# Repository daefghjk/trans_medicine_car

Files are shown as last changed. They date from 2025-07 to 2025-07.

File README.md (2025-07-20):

# 流程
## 基础  
1、小车1上电，摄像头识别初始数字，进入巡线模式，小车1等待药品放入后启动，到达近端病房，等待药品卸载后给摄像头发‘m’，开始返程  
2、同1  
  
## 拓展  
1、小车1上电，摄像头识别初始数字，进入巡线模式，小车1等待药品放入后启动，到达中端病房，检测小车2，等待摄像头发送中端信息‘m‘，小车1判断拓展第几题，发送给小车2；小车2收到后等待药品放入，放入后，且摄像头识别到数字转为巡线模式，开始启动，到1号病房，到了之后点亮黄色LED，发送给小车1，小车1收到信息而且药品卸载后启动返程，发送给小车2熄灭黄色LED，回到药房后发送给小车2，小车2收到后发给摄像头‘m’，走到目标病房。  
  
2、小车1上电，摄像头识别初始数字，进入巡线模式，小车1等待药品放入后启动，到达远端病房，检测小车2，等待摄像头发送远端信息‘f’，小车1判断拓展第几题，发送给小车2；小车2收到后，等待小车1的启动信息，小车1卸载药品后发给摄像头‘m’，开始返程，并发给小车2启动信息，小车2启动，到1号病房等待小车1的启动信息，等到小车1回到药房，发送给小车2启动信息，小车2收到后发给摄像头‘m’，启动到目标病房，亮红色。  
  
拓展1与2的主要差别在：  
1、拓展1小车1需要在小车2到达1号病房后才启动，拓展2小车1不需要等待小车2。  
2、拓展1小车2在小车1未卸载药品就启动，拓展2小车需要等待小车1开始返程才启动。  
  
# K230与小车1与小车2之间的通信协议
K230与小车数据包格式：0xFF、标志位、数据、0xFE  
标志位意义：  
0x00：发送路口方向，此时数据即命令，见下表  
0x01：发送巡线偏移角度，此时数据为字符串形式的浮点数  
0x02：发送到达中端还是远端病房，此时数据即命令，见下表  
  
小车之间数据包格式：0xFF、命令、0xFE  
  
| 方向 | 内容 |
| ---- | ---- |
|车->K230| 0x00 'm' 开启巡线模式|
|K230->车| 0x00 's' 停止电机<br>0x00 'f' 启动电机路口直行<br>0x00 'l' 路口左转<br>0x00 'r' 路口右转<br>0x00 'b' 到达病房<br>0x00 'y' 到达药房<br>0x02 'm' 到达中端病房<br>0x02 'f' 到达远端病|
|小车1->小车2|'1' 目前是拓展1<br>'2' 目前是拓展2<br>'t' 测试是否有小车2<br>'f' 小车2启动<br>'n' 小车2熄灭黄色LED|
|小车2->小车1|'r' 回传确认存在小车2<br>'b' 拓展1确认小车2到达1号病房

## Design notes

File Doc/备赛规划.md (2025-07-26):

## 软件

建个仓库把m0的各种库装进去

直流电机、步进电机、无刷电机、舵机、机械臂

编码器、巡线（灰度）、mpu陀螺仪、

oled、串口屏、

存储器eeprom、

视觉识别（k230、opencv）：颜色形状、误识别、数字（找点例程）、巡线、其他模型的训练和部署

串口、iic、spi、pid、adc、dac、

## 硬件

常见的板子

小车拓展板：4个编码电机、两个舵机、oled、两个串口、陀螺仪、按键和指示灯等，变压

机械臂拓展板：6个舵机/步进电机，

步进电机拓展板：

电源板：引出很多电源线

黑板/红板/嘉立创板之间的转接板

## 机械

问一下能不能借到3d打印机

sw设计

固定k230的支架

机械臂

车架

舵机水平转动的东西

## 其他要买的东西

无线烧录器

考虑一下嘉立创的m0核心板

大车架的常规车轮

## 做题

待选：三子棋、送药小车、激光控制、车位停车

综合测评

用m0做送药小车

研究一下机械臂

## 时间线（暂时）

| 一 | 二 | 三 | 四 | 五 | 六 | 日 |
| ---- | --- | --- | --- | --- | --- | --- |
| | | 2 | 3 | 4 | 5 | 6 |
| | | 今天 | | 研究m0资源和引脚 | 孙艺离开 | 下载程序到m0<br>画拓展板 |
| 7 | 8 | 9 | 10 | 11 | 12 | 13 |
| 视觉 | 视觉 | 视觉<br>把上次的库都拿出来，简单分类 | 孙艺回来 | ，<br>看看freeRTOS， | | |
| | | 16 | | 18 | | 20 |
| | | | 送药小车做完 | 孙艺离开 | | 孙艺回来 |
| | | 23 | | | | |
| | 搞机械臂 | 差不多放元件清单 | | | | |
| | | 30 | 31 | 1 | 2 | 3 |
| | | 开始比赛 | | | 比赛结束 | |

| 模块 | 功能描述 | 具体器件/接口 |
| :---: | :---: | :---: |
| 主控模块 | 系统运算与控制核心 | STM32F103C8T6（ARM Cortex-M3内核） |
| 显示模块 | 时间/日期/闹钟状态可视化 | 8位共阴极LED数码管（动态扫描驱动） |
| 输入模块 | 用户交互入口，支持模式切换、参数校准、闹钟设置 | 4×独立按键（K1-K4）：K1（模式切）、K2（+）、K3（-）、K4（确认） |
| 提醒模块 | 闹钟触发时声音提示 | 无源蜂鸣器（接GPIO输出） |
| 时钟基准 | 提供1Hz计时信号 | 定时器TIM2（配置为1ms中断，累计1000次） |

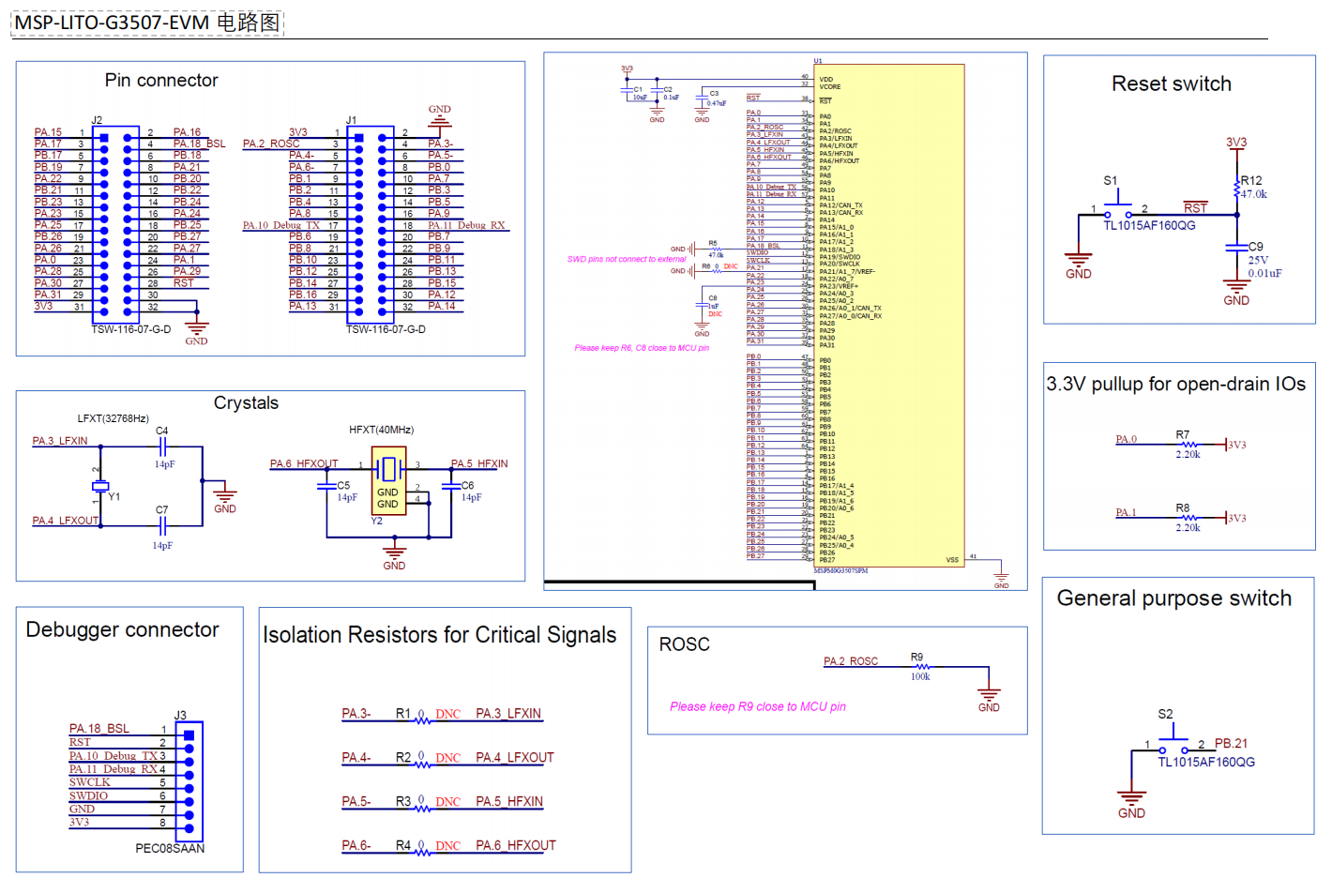
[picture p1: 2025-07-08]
Doc/LITO原理图.png

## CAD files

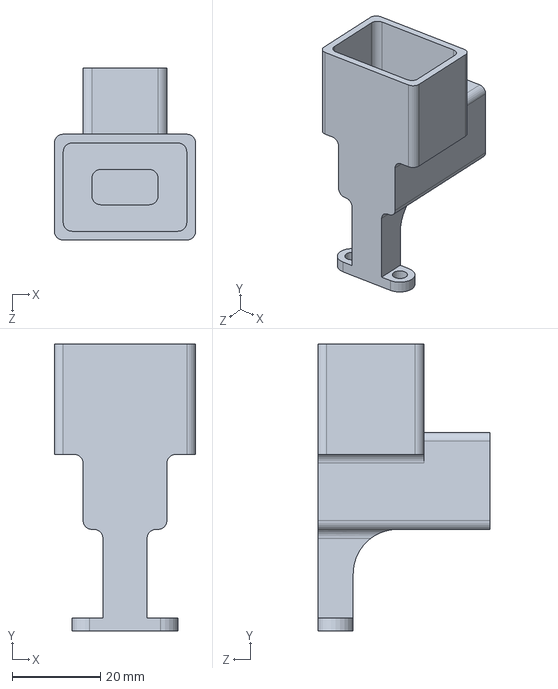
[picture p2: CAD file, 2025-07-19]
2021E硬件/药品放置件.SLDPRT
32.0 x 65.0 x 39.0 mm

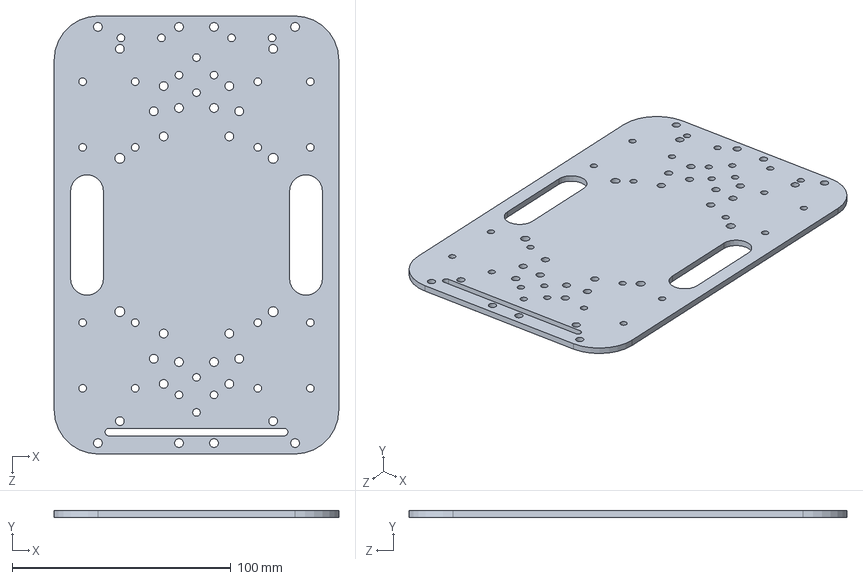
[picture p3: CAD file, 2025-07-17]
2021E硬件/车架.SLDPRT
130.0 x 3.00 x 200.0 mm

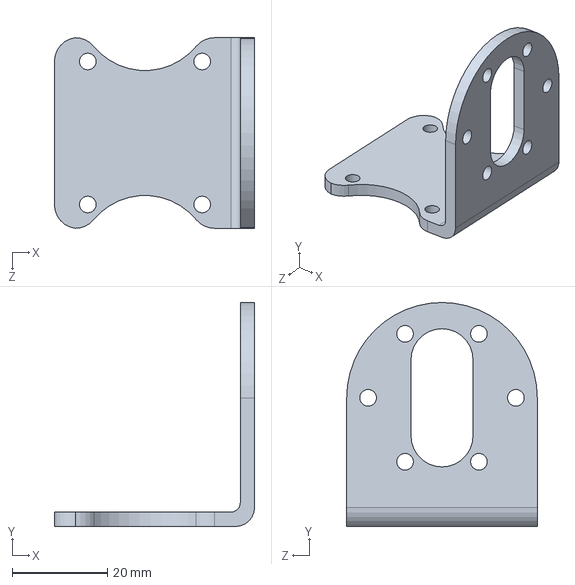
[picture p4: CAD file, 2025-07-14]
2021E硬件/电机固定件.SLDPRT
42.0 x 47.0 x 40.0 mm

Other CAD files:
2021E硬件/电机固定件.3MF
2021E硬件/药品放置件.3MF
2021E硬件/车架.3MF

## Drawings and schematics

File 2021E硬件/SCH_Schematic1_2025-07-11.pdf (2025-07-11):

# LM2596S降压降压

## OUT端5V输出过压保护

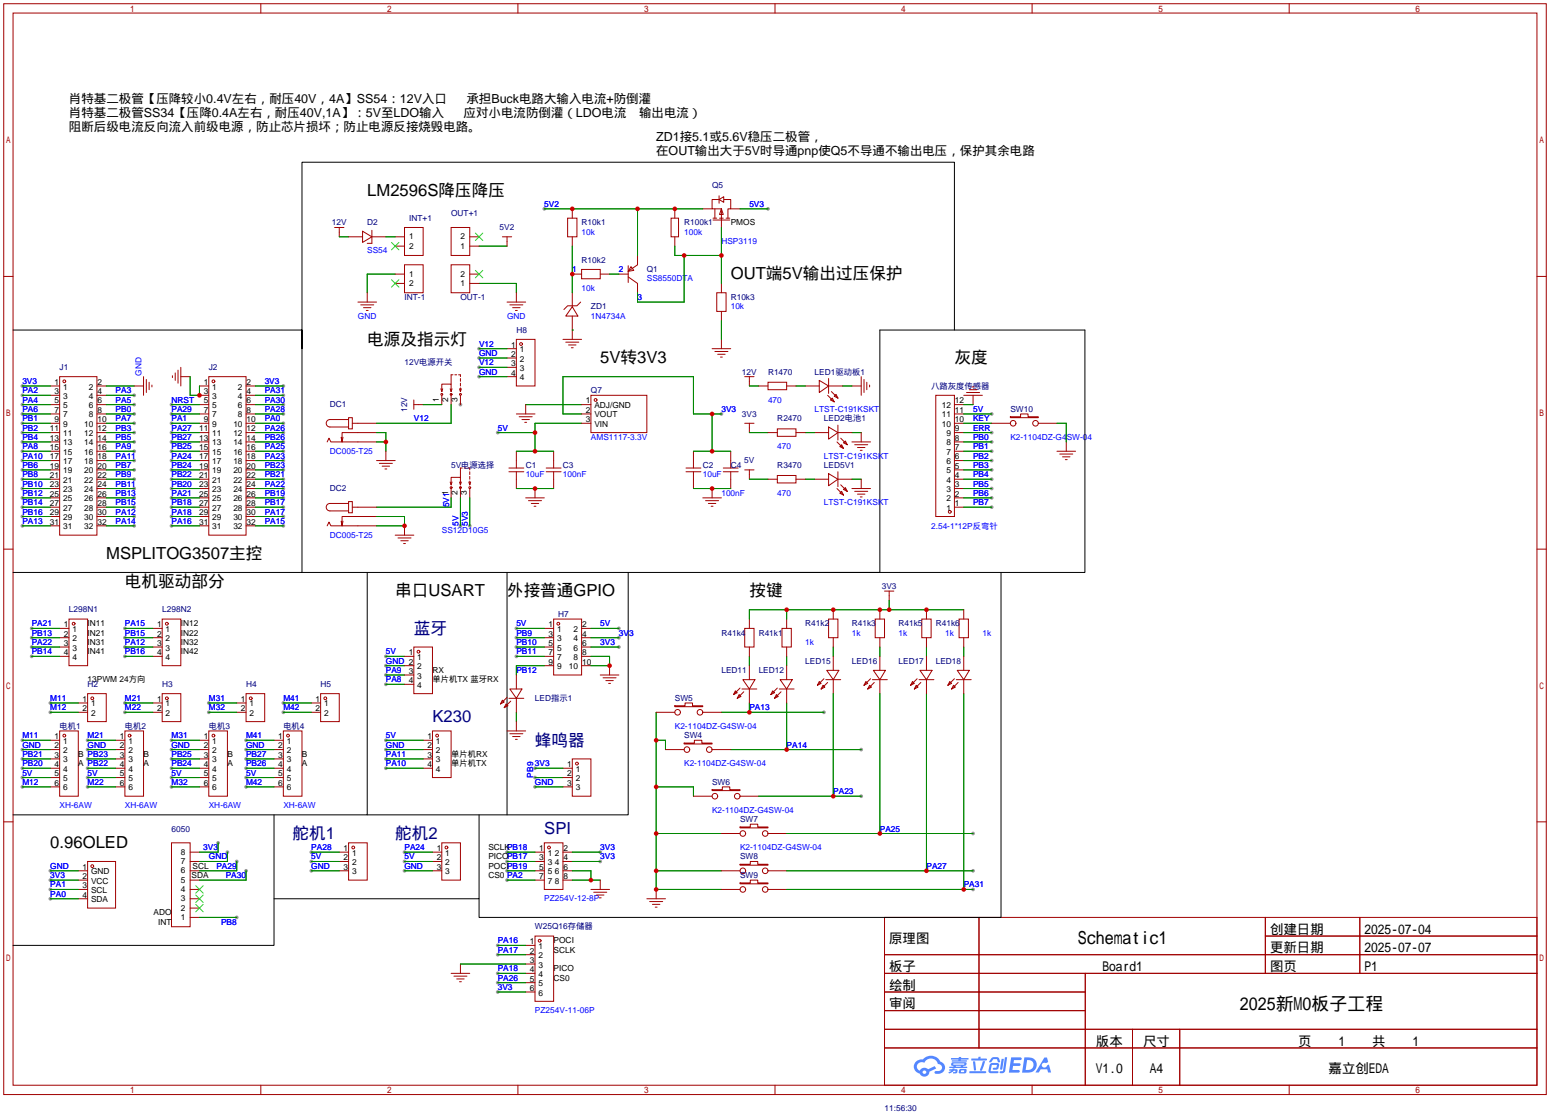
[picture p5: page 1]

原理图 | Schematic1 | 创建日期 | 2025-07-04

更新日期 | 2025-07-07

板子 | Board1 | 图页 | P1
绘制 | | 2025新M0板子工程
审阅

V1.0 | A4 | 嘉立创EDA

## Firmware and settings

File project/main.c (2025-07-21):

#include "BOARD.h"

#define abs(x) (x > 0 ? x : -x)

int32_t CalculatePID(float delta)
{
    static float last_delta = 0;
    int32_t res = Kp * delta + Kd * (delta - last_delta);
    last_delta = delta;
    return res;
}

void Find_Line(void)
{
    int32_t delta_speed = CalculatePID(delta_angle);

    int32_t left_speed = motor_base_speed + delta_speed;
    int32_t right_speed = motor_base_speed - delta_speed;
    if (left_speed > 100) left_speed = 100;
    if (left_speed < 0) left_speed = 0;
    if (right_speed > 100) right_speed = 100;
    if (right_speed < 0) right_speed = 0;

    Motor_SetSpeed(&motor_left, left_speed);
    Motor_SetSpeed(&motor_right, right_speed);
}

void Move_Meter(float meter)
{
    int32_t current_left_count = 0, current_right_count = 0;
    uint8_t dir = meter > 0 ? 1 : 0;
    if (!dir) meter = -meter;
    uint64_t target_count = meter / (3.14159265 * WHELL_DIAMETER / ENCODER_PPR);

    Motor_SetAllDir(MOTOR_DIR_STOP);

    DL_GPIO_disableInterrupt(GPIO_ENCODER_PORT, GPIO_ENCODER_ENCODER_L_A_PIN | GPIO_ENCODER_ENCODER_R_A_PIN);
    left_count = 0;
    right_count = 0;
    DL_GPIO_enableInterrupt(GPIO_ENCODER_PORT, GPIO_ENCODER_ENCODER_L_A_PIN | GPIO_ENCODER_ENCODER_R_A_PIN);

    Motor_SetAllDir(MOTOR_DIR_FORWARD);

    while (1)
    {
        DL_GPIO_disableInterrupt(GPIO_ENCODER_PORT, GPIO_ENCODER_ENCODER_L_A_PIN | GPIO_ENCODER_ENCODER_R_A_PIN);
        current_left_count = left_count;
        current_right_count = right_count;
        DL_GPIO_enableInterrupt(GPIO_ENCODER_PORT, GPIO_ENCODER_ENCODER_L_A_PIN | GPIO_ENCODER_ENCODER_R_A_PIN);

        if ((abs(current_left_count) + abs(current_right_count)) / 2 >= target_count)
            break;

        int32_t delta = 0.5 * (abs(current_left_count) - abs(current_right_count));

        int32_t left_speed = motor_base_speed - delta;
        int32_t right_speed = motor_base_speed + delta;
        if (left_speed > 100) left_speed = 100;
        if (left_speed < 0) left_speed = 0;
        if (right_speed > 100) right_speed = 100;
        if (right_speed < 0) right_speed = 0;

        Motor_SetSpeed(&motor_left, left_speed);
        Motor_SetSpeed(&motor_right, right_speed);

        Delay_ms(10);
    }

    Motor_SetAllDir(MOTOR_DIR_STOP);
}

// angle_deg 大于0向右转
void Rotate_Angle(float angle_deg)
{
    int32_t current_left_count = 0, current_right_count = 0;
    uint8_t dir = angle_deg > 0 ? 1 : 0; //正为右
    if (!dir) angle_deg = -angle_deg;
    float angle_rad = angle_deg * (3.14159265 / 180);
    uint64_t target_count = angle_rad * ROTARY_SHAFT_DIS / (3.14159265 * WHELL_DIAMETER / ENCODER_PPR);

    Motor_SetAllDir(MOTOR_DIR_STOP);

    DL_GPIO_disableInterrupt(GPIO_ENCODER_PORT, GPIO_ENCODER_ENCODER_L_A_PIN | GPIO_ENCODER_ENCODER_R_A_PIN);
    left_count = 0;
    right_count = 0;
    DL_GPIO_enableInterrupt(GPIO_ENCODER_PORT, GPIO_ENCODER_ENCODER_L_A_PIN | GPIO_ENCODER_ENCODER_R_A_PIN);

    if (dir)
    {
        Motor_SetDirection(&motor_left, MOTOR_DIR_FORWARD);
        Motor_SetDirection(&motor_right, MOTOR_DIR_BACKWARD);
    }
    else
    {
        Motor_SetDirection(&motor_left, MOTOR_DIR_BACKWARD);
        Motor_SetDirection(&motor_right, MOTOR_DIR_FORWARD);
    }

    Motor_SetSpeed(&motor_left, 35);
    Motor_SetSpeed(&motor_right, 35);

    while (1)
    {
        DL_GPIO_disableInterrupt(GPIO_ENCODER_PORT, GPIO_ENCODER_ENCODER_L_A_PIN | GPIO_ENCODER_ENCODER_R_A_PIN);
        current_left_count = left_count;
        current_right_count = right_count;
        DL_GPIO_enableInterrupt(GPIO_ENCODER_PORT, GPIO_ENCODER_ENCODER_L_A_PIN | GPIO_ENCODER_ENCODER_R_A_PIN);

        if ((abs(current_left_count) >= target_count ||  abs(current_right_count) >= target_count))
            break;
    }

    Motor_SetAllDir(MOTOR_DIR_STOP);
}

int main(void)
{
    Board_Init();

    while (DL_GPIO_readPins(GPIO_INFRARED_PORT, GPIO_INFRARED_PIN_INFRARED_PIN))
    {
        BLE_SendCmd('t');   //测试是否有小车2
        Delay_ms(100);
        if (ble_flag == 'r')
            mode = EXTRA;
    }
    turn_dir = 'f';

    while (1)
    {
        Key_Num = KEY_GetNum();
        KEY_Act(Key_Num);
        if(Key_Num != 255)
        {
            OLED_ShowNum(2,1,Key_Num,3);
            Servo_SetAngle( Key_Num*20);
            // OLED_ShowNum(3,2,servo1.current_angle,3);
        }
        Key_Num = 255;
        
        OLED_ShowChar(1, 1, turn_dir);

        switch (turn_dir)
        {
            case 's':
                Motor_SetAllDir(MOTOR_DIR_STOP);
                find_line_en = 0;
                break;
            case 'f':
                Motor_SetAllDir(MOTOR_DIR_FORWARD);
                find_line_en = 1;
                break;
            case 'l':
                DL_UART_Main_disableInterrupt(K230_INST, DL_UART_MAIN_INTERRUPT_RX);
                find_line_en = 0;
                Move_Meter(0.4);
                Rotate_Angle(-120);
                Motor_SetAllDir(MOTOR_DIR_FORWARD);
                turn_dir = 'f';
                find_line_en = 1;
                DL_UART_Main_enableInterrupt(K230_INST, DL_UART_MAIN_INTERRUPT_RX);
                break;
            case 'r':
                DL_UART_Main_disableInterrupt(K230_INST, DL_UART_MAIN_INTERRUPT_RX);
                find_line_en = 0;
                Move_Meter(0.43);
                Rotate_Angle(120);
                Motor_SetAllDir(MOTOR_DIR_FORWARD);
                turn_dir = 'f';
                find_line_en = 1;
                DL_UART_Main_enableInterrupt(K230_INST, DL_UART_MAIN_INTERRUPT_RX);
                break;
            case 'b':
                while (mode == EXTRA);  //等待k230回传得到目前是什么模式
                DL_UART_Main_disableInterrupt(K230_INST, DL_UART_MAIN_INTERRUPT_RX);
                find_line_en = 0;
                Move_Meter(0.3);
                Rotate_Angle(240);
                DL_GPIO_setPins(GPIO_LED_PIN_RED_PORT, GPIO_LED_PIN_RED_PIN);
                if (mode == EXTRA_1)    
                {
                    BLE_SendCmd('f');       //启动小车2到1号病房
                    while (ble_flag != 'b');//拓展第一题需要等待小车2到达1号病房，不然会撞车
                }
                while (!DL_GPIO_readPins(GPIO_INFRARED_PORT, GPIO_INFRARED_PIN_INFRARED_PIN));
                if (mode == EXTRA_1)    //拓展第一题小车1返程需要告诉小车2熄灭黄色LED
                    BLE_SendCmd('n');
                if (mode == EXTRA_2)    //拓展第二题在小车1启动返程后就让小车2到1号病房
                    BLE_SendCmd('f');
                DL_GPIO_clearPins(GPIO_LED_PIN_RED_PORT, GPIO_LED_PIN_RED_PIN);
                K230_SendCmd('m');
                turn_dir = 'f';
                find_line_en = 1;
                DL_UART_Main_enableInterrupt(K230_INST, DL_UART_MAIN_INTERRUPT_RX);
                break;
            case 'y':
                DL_UART_Main_disableInterrupt(K230_INST, DL_UART_MAIN_INTERRUPT_RX);
                find_line_en = 0;
                Move_Meter(0.2);
                Motor_SetAllDir(MOTOR_DIR_STOP);
                DL_GPIO_setPins(GPIO_LED_PIN_GREEN_PORT, GPIO_LED_PIN_GREEN_PIN);
                if (mode == EXTRA_1 || mode == EXTRA_2) //拓展在小车1回到药房后才使小车2从1号病房启动
                    BLE_SendCmd('f');
                turn_dir = '0';
                DL_UART_Main_enableInterrupt(K230_INST, DL_UART_MAIN_INTERRUPT_RX);
                break;
            default:
                break;
        }

        if (find_line_en) Find_Line();
    }
}

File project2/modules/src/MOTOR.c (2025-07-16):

#include <ti/driverlib/dl_timera.h>
#include <ti/driverlib/dl_timerg.h>
#include <ti/driverlib/dl_gpio.h>
#include "MOTOR.h"

void PWM_SetDuty(GPTIMER_Regs *gpt, DL_TIMER_CC_INDEX ccIndex, uint32_t duty_percent)
{
    uint32_t load = DL_Timer_getLoadValue(gpt);
    uint32_t outCtl = DL_Timer_getCaptureCompareOutCtl(gpt, ccIndex);
    DL_TIMER_COUNT_MODE mode = DL_Timer_getCounterMode(gpt);

    // 是否翻转，不翻转在cmpx前是高电平，翻转在cmpx前是低电平
    uint8_t isInverted = (outCtl & DL_TIMER_CC_OCTL_INV_OUT_ENABLED);

    if (duty_percent > 100) duty_percent = 100;
    uint32_t highTime = ((load + 1) * duty_percent) / 100;

    uint32_t cmpx;

    switch (mode)
    {
        case DL_TIMER_COUNT_MODE_UP:
            cmpx = isInverted ? (load + 1 - highTime) : highTime;
            break;

        case DL_TIMER_COUNT_MODE_DOWN:
            cmpx = isInverted ? highTime : (load + 1 - highTime);
            break;

        case DL_TIMER_COUNT_MODE_UP_DOWN:
            highTime = (2 * (load + 1) * duty_percent) / 100;
            cmpx = isInverted ? (load + 1 - highTime / 2) : (highTime / 2);
            break;

        default:
            // 默认按 DOWN 模式处理
            cmpx = isInverted ? highTime : (load + 1 - highTime);
            break;
    }

    DL_Timer_setCaptureCompareValue(gpt, cmpx - 1, ccIndex);
}

void Motor_SetSpeed(Motor_Handle *motor, int16_t percent)
{
    if (percent > 100) percent = 100;
    if (percent < 0) percent = 0;
    motor->current_speed = percent;

    uint32_t effective_percent;
    switch (motor->current_dir)
    {
        case MOTOR_DIR_FORWARD:
        case MOTOR_DIR_STOP:
            effective_percent = percent;
        break;

        case MOTOR_DIR_BACKWARD:
            effective_percent = 100 - percent;
        break;

        default:
            effective_percent = percent;
        break;
    }

    PWM_SetDuty(motor->timer_base, motor->pwm_channel, effective_percent);
}

void Motor_SetDirection(Motor_Handle *motor, Motor_DirectionType dir)
{
    motor->current_dir = dir;

    switch (dir)
    {
        case MOTOR_DIR_FORWARD:
            DL_GPIO_clearPins(motor->in2_port, motor->in2_pin);
            Motor_SetSpeed(motor, motor->current_speed);
            break;
        case MOTOR_DIR_BACKWARD:
            DL_GPIO_setPins(motor->in2_port, motor->in2_pin);
            Motor_SetSpeed(motor, motor->current_speed);
            break;
        case MOTOR_DIR_STOP:
        default:
            DL_GPIO_clearPins(motor->in2_port, motor->in2_pin);
            Motor_SetSpeed(motor, 0);
            break;
    }
}

void Motor_Init(Motor_Handle *motor)
{
    Motor_SetDirection(motor, motor->current_dir);
    Motor_SetSpeed(motor, motor->current_speed);
}

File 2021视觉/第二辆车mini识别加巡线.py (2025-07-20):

'''
A. 上电/复位后
进入MODE_DETECTION（识别模式），识别初始数字。
识别到初始数字后，自动进入拓展模式（MODE_EXPAND），cross_count清零。
B. 拓展模式（MODE_EXPAND）
只巡线，不识别。
第一个路口强制左转（发送'l'），不入栈（去程）。
继续巡线，遇终点（小黑块+红线消失）停下，发s，进入MODE_NONE，cross_count清零。
C. 拓展返程模式（MODE_EXPAND，expand_after_m=True）
收到第一个m后，发f，进入拓展返程模式。
只巡线，第一个路口强制左转，入栈一个'f'，然后切回MODE_LINE（普通巡线识别模式）。
后续每遇路口，先停车，切换到识别模式，识别数字，决策后入栈（如'l'/'r'/'f'），再巡线。
终点检测到小黑块+红线消失，发s，进入MODE_NONE。
D. 普通返程模式（MODE_LINE，returning=True）
收到第二个m后，发f，进入普通返程模式，returning=True，return_count=cross_count。
每遇路口，先停车，出栈，取反方向（l↔r，f不变），发送后继续巡线，return_count递减。
终点检测到小黑块+红线消失，发y，流程结束。
E. 普通去程模式（MODE_LINE）
每遇路口，先停车，切换到识别模式，识别数字，决策后入栈（l/r/f），再巡线。
终点检测到小黑块+红线消失，发b，进入MODE_NONE。
F. 无模式（MODE_NONE）
任何模式下遇终点后，进入无模式，等待单片机发来m指令。
第一次收到m，发f，进入拓展返程模式。
第二次收到m，发f，进入普通返程模式。
G. 按键复位
任意时刻按下按键，系统复位，所有状态变量清零，回到初始识别模式。
'''
import gc
import os
import time
import math

import aicube
import image
import nncase_runtime as nn
import ujson
import ulab.numpy as np
# from libs.PipeLine import ScopedTiming
from libs.Utils import *
from media.display import *
from media.media import *
from media.sensor import *
from machine import UART
from machine import FPIOA
from machine import Pin

# 配置参数
display_mode = "lcd"
DISPLAY_WIDTH = 640
DISPLAY_HEIGHT = 480
OUT_RGB888P_WIDTH = 640
OUT_RGB888P_HEIGH = 480

# AI识别配置
root_path = "/sdcard/mp_deployment_source/"
config_path = root_path + "deploy_config.json"
debug_mode = 1

# 巡线阈值（LAB空间，适用于RGB565）
BLACK_THRESHOLD = [(0, 40, -128, 127, -128, 127)]  # 黑线阈值
RED_THRESHOLD = [(20, 60, 20, 127, 20, 127)]      # 红线阈值
# 蓝线
# LINE_THRESHOLD = [(0, 50, -128, 0, -128, 0)]
# LINE_THRESHOLD = [(20, 60, 10, 127, 10, 127)]  # 默认黑线

# ROI区域配置 (x, y, w, h, weight)
ROIS = [
    (0, 400, 800, 80, 0.6),   # 下方
    (0, 240, 800, 80, 0.3),   # 中间
    (0, 80, 800, 80, 0.1)     # 上方
]

weight_sum = sum(r[4] for r in ROIS)

# 功能开关（由状态机自动控制，不手动设置）
# ENABLE_LINE_FOLLOW = False    # 是否启用巡线
# ENABLE_DETECTION = True      # 是否启用AI识别

# 模式状态
MODE_DETECTION = 0
MODE_LINE = 1
MODE_EXPAND = 2  # 拓展模式
MODE_NONE = 3    # 无模式
mode = MODE_DETECTION
pause_for_m = False

# 识别模式相关变量
first_number = None
number_list = []
detect_count = 0
max_detect_count = 8
match_found = False
match_direction = None

# 返程相关变量
returning = False
return_count = 0
return_direction = None
last_match_direction = None

# 用于延时切换模式
import utime as time_mod
mode_switch_time = 0
mode_pause = False
pause_duration = 0

# 串口通信内容显示缓存
uart_last_send = ""
uart_last_recv = ""
uart_last_send_meaning = ""
uart_last_recv_meaning = ""
# 识别显示缓存
last_detected_number = ""
last_match_result = ""

# 路口转向栈
turn_stack = []

# 按键初始化，GPIO21，如无反应可尝试其他引脚
button = Pin(21, Pin.IN, Pin.PULL_UP)

# 串口接收缓冲区（修复NameError）
uart_rx_buf = bytearray()

def two_side_pad_param(input_size, output_size):
    ratio_w = output_size[0] / input_size[0]
    ratio_h = output_size[1] / input_size[1]
    ratio = min(ratio_w, ratio_h)
    new_w = int(ratio * input_size[0])
    new_h = int(ratio * input_size[1])
    dw = (output_size[0] - new_w) / 2
    dh = (output_size[1] - new_h) / 2
    top = int(round(dh - 0.1))
    bottom = int(round(dh + 0.1))
    left = int(round(dw - 0.1))
    right = int(round(dw - 0.1))
    return top, bottom, left, right, ratio

def read_deploy_config(config_path):
    with open(config_path, "r") as json_file:
        try:
            config = ujson.load(json_file)
        except ValueError as e:
            print("JSON 解析错误:", e)
    return config
'''
def send_uart_number(uart, number, confidence):
    """串口发送数字和置信度"""
    send_data = bytearray([0xFF, ord(number[0]), int(confidence * 100), 0xFE])
    uart.write(send_data)
    print("send")
'''
def send_uart_cmd(uart, flag, cmd=None):
    global uart_last_send
    if flag == 0x00:
        uart_last_send = cmd
        data = bytearray([0xFF, 0x00, ord(cmd), 0xFE])
        uart.write(data)
    elif flag == 0x01:
        uart_last_send = "angle"
        str_val = "{:.1f}".format(-cmd)  # 保留一位小数
        str_bytes = str_val.encode()    # 转为字节流
        data = bytearray([0xFF, 0x01]) + str_bytes + bytearray([0xFE])
        uart.write(data)
    print(f"TX: {uart_last_send}")
#先将浮点数格式化为字符串（保留一位小数），
#再转为字节流发送（encode()），
#最终数据包格式为 [0xFF, 0x01] + str_bytes + [0xFE]。
def line_detection(img, osd_img=None):
    """巡线检测函数，支持在osd_img上画框"""
    centroid_sum = 0
    cross_detected = False
    rects = []
    threshold = RED_THRESHOLD  # 巡线改为红线阈值
    use_color = True
    roi_valid = [True, True, True]
    roi_centers = [None, None, None]
    roi_weights = [r[4] for r in ROIS]
    overwide_count = 0
    OVERWIDE_THRESH = 120  # 红线过宽阈值，可根据实际调整

    for idx, r in enumerate(ROIS):
        blobs = img.find_blobs(threshold, roi=r[0:4], merge=True, color=use_color)
        if blobs:
            largest_blob = max(blobs, key=lambda b: b.pixels())
            rects.append(largest_blob.rect())
            w = largest_blob.w()
            if w > OVERWIDE_THRESH:
                roi_valid[idx] = False
                overwide_count += 1
            else:
                roi_centers[idx] = largest_blob.cx()
            # 路口检测：只用最上面ROI的宽色块
            if idx == 2 and w > 400:
                cross_detected = True
        else:
            rects.append(None)
            roi_valid[idx] = False

    # 只用不过宽的红线块计算偏移角度
    if overwide_count < 3:
        valid_sum = sum(roi_weights[i] for i in range(3) if roi_valid[i])
        centroid_sum = sum((roi_centers[i] or 0) * roi_weights[i] for i in range(3) if roi_valid[i])
        center_pos = (centroid_sum / valid_sum) if valid_sum > 0 else 400
        deflection_angle = -math.atan((center_pos - 400) / 240)
        deflection_angle = math.degrees(deflection_angle)
    else:
        deflection_angle = 0  # 或None，表示不计算

    # 在osd_img上画出每个ROI的检测框
    if osd_img is not None:
        for idx, r in enumerate(ROIS):
            if rects[idx] is not None:
                x, y, w, h = rects[idx]
                osd_img.draw_rectangle(x, y, w, h, color=(255,255,255), thickness=3)
                osd_img.draw_cross(x+w//2, y+h//2, color=(255,255,255), size=32, thickness=3)
    return deflection_angle, cross_detected

# ========== 功能函数封装 ========== #

def reset_all_status():
    """一键复位，重置所有状态变量"""
    global mode, first_number, number_list, detect_count, match_found, match_direction, mode_switch_time, mode_pause, pause_duration, pause_for_m, returning, return_count, return_direction, last_match_direction, last_detected_number, last_match_result, turn_stack, uart_last_send, uart_last_recv
    mode = MODE_DETECTION
    first_number = None
    number_list = []
    detect_count = 0
    match_found = False
    match_direction = None
    mode_switch_time = 0
    mode_pause = False
    pause_duration = 0
    pause_for_m = False
    returning = False
    return_count = 0
    return_direction = None
    last_match_direction = None
    last_detected_number = ""
    last_match_result = ""
    turn_stack.clear()
    uart_last_send = ""
    uart_last_recv = ""
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

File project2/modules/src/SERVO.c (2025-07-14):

#include "ti_msp_dl_config.h"
#include "SERVO.h"

float Servo_Angle_TurnMin;//每�?�变化的角度
float Servo_Angle;


void Servo_SetAngle(float Angle)	//设置角度,0-180
{
    if(Angle >= 180)
    {
        Servo_SetAngle(Angle - 180); 
    }
    else if (Angle < 0) 
    {
        Servo_SetAngle(Angle + 180);
    }
    else
    {
        Servo_Angle = Angle;
        DL_TimerA_setCaptureCompareValue(SERVO_INST, 975 - Angle * 100 / 180, GPIO_SERVO_C1_IDX);
    }
}

void Servo_Angle_Limit(void)		//限制角度��?60-120
{
	if(Servo_Angle >= 120)
	{
		Servo_Angle = 120;
	}
	
	if(Servo_Angle <= 60)
	{
		Servo_Angle = 60;
	}
}

void Servo_Turn_Right(float Angle_Turn)
{
	Servo_Angle += Angle_Turn;
	Servo_Angle_Limit();//限幅
	Servo_SetAngle(Servo_Angle);
}

void Servo_Turn_Left(float Angle_Turn)
{
	Servo_Angle -= Angle_Turn;
	Servo_Angle_Limit();//限幅
	Servo_SetAngle(Servo_Angle);
}

void Servo_Turn_Stright(float Angle_Turn)
{
	if(Servo_Angle > 90)
	{
		Servo_Turn_Left(Angle_Turn);
	}
	
	else if(Servo_Angle < 90)
	{
		Servo_Turn_Right(Angle_Turn);
	}
	
	Servo_SetAngle(Servo_Angle);
}

//ת��
void Servo_Angle_Turn(float Angle_Turn)
{
	if(Servo_Angle < 0)
	{
		Servo_Turn_Left(Angle_Turn);
	}
	
	else if(Servo_Angle > 0)
	{
		Servo_Turn_Right(Angle_Turn);
	}
}

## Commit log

2025-07-05 初始化工程
2025-07-07 新增了LITOMO拓展板第一版
2025-07-08 增加OLED驱动库，增加核心板原理图
2025-07-08 更正gitignore位置，添加芯片手册
2025-07-08 添加了视觉识别K230代码及kmodel文件
2025-07-09 修复OLED驱动bug
2025-07-09 修正了syscfg的编译器
2025-07-10 增加电机驱动（未调试），添加LaunchPad手册
2025-07-10 增加了delay和key
2025-07-11 修复电机驱动库bug
2025-07-11 非阻塞式的key，可长按短按双击
2025-07-11 servo没写好先不要用
2025-07-12 根据板子原理图修改syscfg，固定部分gpio
2025-07-12 把全局变量和初始化放在BOARD中
2025-07-12 修点小bug
2025-07-12 添加车架
    [车架.3MF, 车架.SLDPRT]
2025-07-13 添加电机固定件
    [电机固定件.3MF, 电机固定件.SLDPRT]
2025-07-13 servo对了，规范化再说吧~
2025-07-14 添加最新K230识别加巡线代码
2025-07-14 添加与k230的串口通信，添加pd循迹（都未调试），修改电机固定件
    [电机固定件.3MF, 电机固定件.SLDPRT]
2025-07-15 完成与k230的循迹通信，循迹参数未调
2025-07-15 完成了与K230在路口的通信，转弯的方式还在考虑
2025-07-15 小调了一下巡线pid参数
2025-07-16 完成了编码器部分，基本完成了转向，但转向由于四驱出现抖动，待解决
2025-07-17 四驱确定不行，准备换万向轮，添加新车架
    [车架.3MF, 车架.SLDPRT]
2025-07-17 添加新车架和药品放置件
    [药品放置件.3MF, 药品放置件.SLDPRT, 车架.3MF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]
2025-07-17 最新视觉代码
2025-07-17 可以正常使用的代码
2025-07-18 改为三轮小车
    [药品放置件.3MF, 药品放置件.SLDPRT]
2025-07-18 基础部分基本完成，添加了与小车2的蓝牙部分，以及当前所处题目的识别
2025-07-18 让ai重构k230代码
2025-07-19 新增天猛星拓展板
2025-07-19 添加小车2工程
    [药品放置件.3MF, 药品放置件.SLDPRT]
2025-07-19 添加流程设计
2025-07-20 更新 README.md
2025-07-20 完成小车1逻辑，添加了通信协议表
2025-07-20 完成小车2逻辑
2025-07-20 添加代码一二辆车的代码
2025-07-21 已经完成题目要求所有功能，巡线参数还可以调一调
2025-07-22 第二辆车代码更新
2025-07-22 第二辆车代码更新2
2025-07-26 Update 题目说明
